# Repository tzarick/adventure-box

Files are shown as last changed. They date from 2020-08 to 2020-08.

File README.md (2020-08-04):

# adventure-box

A box that only opens / unlocks when it arrives at specific geographic coordinates.

## Disclaimer

If you are one of the few people I gave one of these boxes to and you still haven't reached your destination _and_ you somehow found this... 1) get a move on with it smh, and 2) leave now!!! Be gone! Mild spoilers live here.

## Background

This project was made as a Christmas gift for each member (each couple, technically) of my family: a lockbox that is locked when they unwrap it and only openable once they take it with them to some specific location on the globe. I thought it would be a fun reverse geocache / scavenger hunt.

I like the idea of "opening" the box as an adventure / experience rather than seeing it as just a thing in a box that requires some extra work to open.

## Functionality

The small display on the outside of the box shows:

1. the **distance** in miles away from the destination, and
2. the **heading** in degrees that you need to proceed in

This specific program currently takes in 2 sets of coordinates:

1. a final destination, and
2. a checkpoint

Initially, the checkpoint is treated as the destination (the user should not know this, as all they see is a distance and heading, and know that they need to take the box somewhere). At the checkpoint, there was a physical clue in real life which eventually prompted them to interact with the box in a way that passes the checkpoint and reveals their new distance and heading (to the final destination).

Upon arrival at the final destination, the 3-digit box combination is displayed on-screen.

## Hardware / Parts

Main box components:

- 3-digit combination aluminum lockbox
- 128 x 64 OLED display
- NEO-6M GPS module + antenna
- Arduino Pro Mini 5V
- Piezo buzzer
- Push button
- Power switch
- Small 5V/1A power bank
- USB charging cable

I'll include a full list of the specific parts I used at a later time (TODO).

## Software

I consulted some examples / projects from the NEO-6M GPS module and projects that involve both GPS module and small I2C OLED display. I also found some specific piezo buzzer note encodings and a short sequence or two online. Will include specific references at a later time (TODO).

Am going to clean up the code a bit, hopefully soon (TODO).

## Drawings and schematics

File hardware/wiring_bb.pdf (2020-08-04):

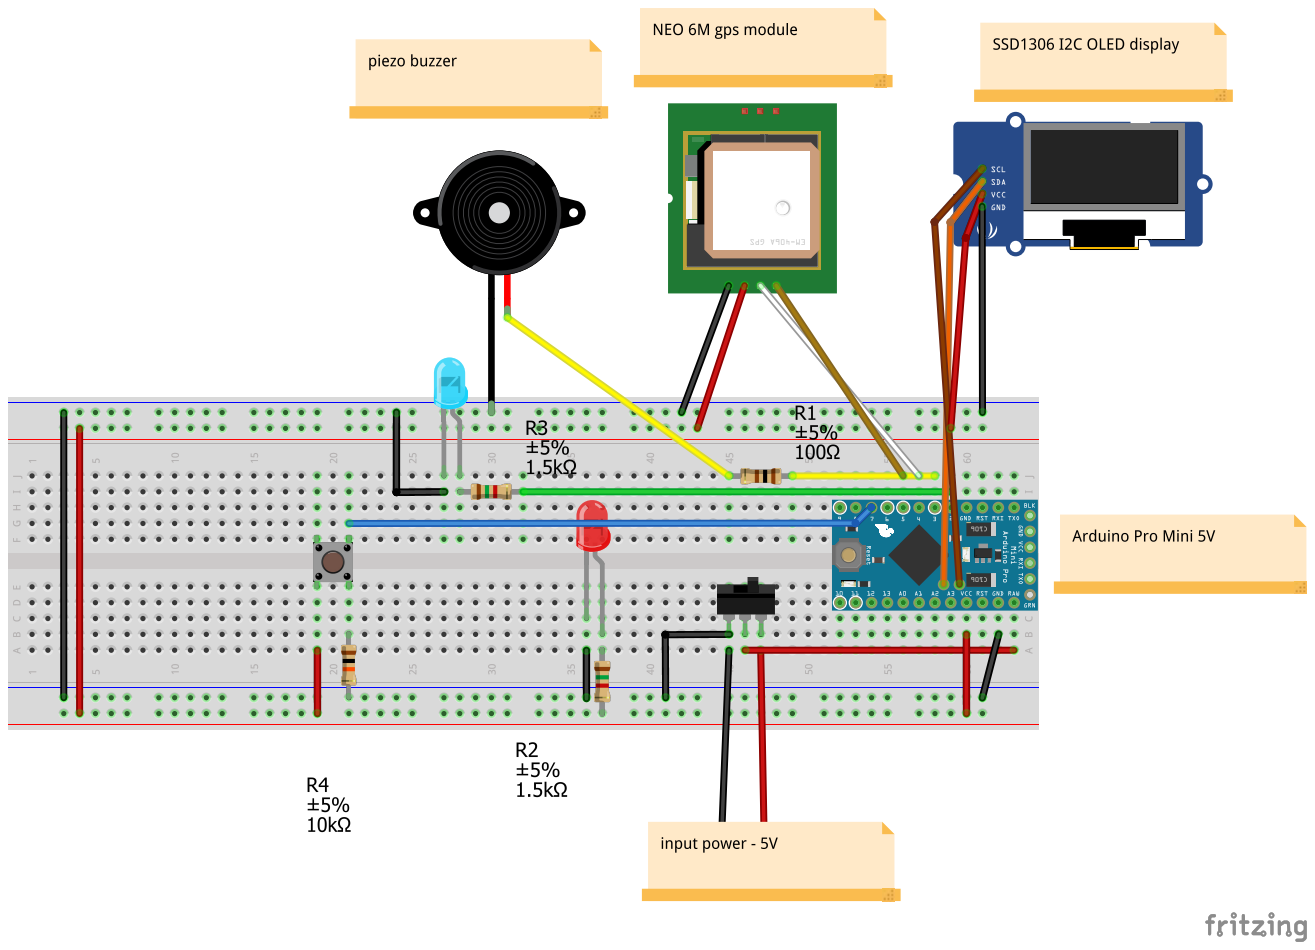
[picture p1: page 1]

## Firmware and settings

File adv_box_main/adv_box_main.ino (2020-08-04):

#include <EEPROM.h>
#include <TinyGPS++.h>
#include <SoftwareSerial.h>
//#include <AltSoftSerial.h>
//#include <SPI.h>
#include <Wire.h>
#include <Arduino.h>
#include <U8x8lib.h>

#ifdef U8X8_HAVE_HW_SPI
#include <SPI.h>
#endif

// chest sound params
int speakerPin = 3;
const int switchPin = 1;
const int buttonPin = 7;
const int fixLed = 2;

char notes[] = "gabygabyxzCDxzCDabywabywzCDEzCDEbywFCDEqywFGDEqi        azbC"; // a space represents a rest
int length = sizeof(notes); // the number of notes
int beats[] = { 1,1,1,1, 1,1,1,1, 1,1,1,1, 1,1,1,1, 1,1,1,1, 1,1,1,1, 1,1,1,1, 1,1,1,1, 1,1,1,1, 1,1,1,1, 1,1,1,1, 1,1,1,1, 1,1,1,1, 1,1,1,1, 2,3,3,16,};
int tempo = 75;

char notes_poke_heal[] = "bbbgG";
int length_poke = sizeof(notes_poke_heal);
int beats_poke_heal[] = { 4,4,2,2,3 };
int tempo_poke = 80;

enum { // distance status
  ACQUIRING,
  RLY_FAR,
  FAR,
  CLOSER,
  ON_FIRE,
  ARRIVED
};

enum { // journey_status
  XMAS_MORN,
  NO_PROGRESS,
  CHECKPOINT_ARRIVED,
  CHECKPOINT_COMPLETED,
  DESTINATION_ARRIVED
};


int cur_status = ACQUIRING;

int journey_status = EEPROM.read(0); // last session's arrival status is saved in addr 0 of EEPROM --> already fully completed journey if this loc contains DESTINATION_ARRRIVED (3)

// gps setup
SoftwareSerial ss(4,5);
//AltSoftSerial altSerial;
TinyGPSPlus gps;

// display init
U8X8_SSD1306_128X64_NONAME_SW_I2C u8x8(/* clock=*/ SCL, /* data=*/ SDA, /* reset=*/ U8X8_PIN_NONE);   // OLEDs without Reset of the Display

// coords define
#define CHECKPOINT_LAT 00.00000   // actual coords redacted !
#define CHECKPOINT_LNG 00.00000
#define FINAL_LAT 00.0000
#define FINAL_LNG 00.00000

#define COMBINATION XXX // combination to the three number lock box code. actual combination redacted !

#define UNIQUE_BUTTON_HOLD_TIME 7000  // this is the amount of time (ms) the button needs to be held to pass the 1st first checkpoint (when in proximity of the checkpoint location)

#define milesInKm 0.62137119223
#define feetInMile 5280.0

const double checkpointTarget[2] = {CHECKPOINT_LAT, CHECKPOINT_LNG};
const double finalTarget[2] = {FINAL_LAT, FINAL_LNG};
bool flag_checkpoint_just_completed = false;
double targetLat;
double targetLng;



void playTone(int tone, int duration) {
  for (long i = 0; i < duration * 1000L; i += tone * 2) {
    digitalWrite(speakerPin, HIGH);
    delayMicroseconds(tone);
    digitalWrite(speakerPin, LOW);
    delayMicroseconds(tone);
  }
}

void playNote(char note, int duration) {
  char names[] = { 'c', 'd', 'e', 'f', 'g', 'x', 'a', 'z', 'b', 'C', 'y', 'D', 'w', 'E', 'F', 'q', 'G', 'i' };
  // c=C4, C = C5. These values have been tuned.
  int tones[] = { 1898, 1690, 1500, 1420, 1265, 1194, 1126, 1063, 1001, 947, 893, 843, 795, 749, 710, 668, 630, 594 };
   
  // play the tone corresponding to the note name
  for (int i = 0; i < 18; i++) {
    if (names[i] == note) {
      playTone(tones[i], duration);
    }
  }
}

void playChestSound() {
    if (digitalRead(switchPin) == 1) {
      for (int i = 0; i < length; i++) {
        if (notes[i] == ' ') {
          delay(beats[i] * tempo); // rest
        } else {
          playNote(notes[i], beats[i] * tempo);
        }
          
        // pause between notes
        delay(tempo / 2); 
    }
  }
}

void playPokeSound() {
    if (digitalRead(switchPin) == 1) {
    for (int i = 0; i < length_poke; i++) {
      if (notes_poke_heal[i] == ' ') {
        delay(beats_poke_heal[i] * tempo); // rest
      } else {
        playNote(notes_poke_heal[i], beats_poke_heal[i] * tempo_poke);
      }
        
      // pause between notes
      delay(tempo_poke / 2); 
    }
  }
}


void arrivalRoutine() {
  playChestSound();
  digitalWrite(fixLed, LOW);
  // display combination
  u8x8.setCursor(0,4);
  u8x8.print("Code:");
  u8x8.setCursor(6,4);
  u8x8.print(COMBINATION);
}


void setup() {
//  EEPROM.write(0,0);
  u8x8.begin(); // display setup
  u8x8.setPowerSave(0); 
  u8x8.setFont(u8x8_font_chroma48medium8_r);
  

  if (journey_status != DESTINATION_ARRIVED) {
      Serial.begin(9600);
    //  if(!display.begin(SSD1306_SWITCHCAPVCC, 0x3C)) {
    //    Serial.println(F("SSD1306 display screen allocation failed"));
    //  }
      Serial.println("start");
      targetLat = (journey_status >= CHECKPOINT_COMPLETED) ? finalTarget[0] : checkpointTarget[0];
      targetLng = (journey_status >= CHECKPOINT_COMPLETED) ? finalTarget[1] : checkpointTarget[1];

    //  altSerial.begin(9600);
      ss.begin(9600);

       if (journey_status == XMAS_MORN) {
          u8x8.print("Merry X-mas");
          u8x8.setCursor(0,1);
          u8x8.print("Nicky & Liv!! :)");
          u8x8.setCursor(0,4);
          u8x8.print("Love, Tommy");
       }
       else if (journey_status == CHECKPOINT_ARRIVED) { // arrived at checkpoint but haven't completed it yet
          u8x8.drawString(0,0,"Acquiring...");
          u8x8.setCursor(0,4);
          u8x8.print("You made it!");
          u8x8.setCursor(0,5);
          u8x8.setInverseFont(1);
          u8x8.print("go down ravine.");
          u8x8.setInverseFont(0);
          u8x8.setCursor(0,6);
          u8x8.print("Enter the mouth");
          u8x8.setCursor(0,7);
          u8x8.print("50 paces 4 hint");
      }
      else {
        u8x8.drawString(0,0,"Acquiring...");
      }
      
      u8x8.refreshDisplay();  
    
    
      pinMode(speakerPin, OUTPUT);
      pinMode(switchPin, INPUT);
      pinMode(fixLed, OUTPUT);
      digitalWrite(fixLed, LOW);
      digitalWrite(switchPin, HIGH);
  }
  else { // game over from here on out forever

      u8x8.print("You rock!");
      u8x8.setCursor(0,2);
      u8x8.print("Merry Xmas :)");
      u8x8.setCursor(0,4);
      u8x8.print("Code:");
      u8x8.setCursor(6,4);
      u8x8.print(COMBINATION);
      while(1); // nothing forever
  }


}

void loop() {
    digitalWrite(fixLed, LOW);
    
    if (journey_status == XMAS_MORN && digitalRead(buttonPin) == HIGH) { // xmas morning initial button press
      journey_status = NO_PROGRESS;
      EEPROM.write(0,journey_status);

      // update display
      u8x8.clear();
      u8x8.drawString(0,0,"Acquiring...");
      u8x8.refreshDisplay();
    }
    
    unsigned long button_press_instant = millis(); 
    while (journey_status == CHECKPOINT_ARRIVED && digitalRead(buttonPin) == HIGH) {
      if (millis() - button_press_instant > UNIQUE_BUTTON_HOLD_TIME) { // checkpoint complete!!
        ss.end(); // stop bc of interference with pwm/buzzer
        
        playPokeSound();
        
        ss.begin(9600);
        
        // update destination and journey status
        journey_status = CHECKPOINT_COMPLETED;
        EEPROM.write(0, journey_status);
        flag_checkpoint_just_completed = true;
        
        targetLat = finalTarget[0];
        targetLng = finalTarget[1];
        
        // update display with the limited amount of characters we have to work with on this tiny display
        u8x8.clearLine(4);
        u8x8.clearLine(5);
        u8x8.clearLine(6);
        u8x8.clearLine(7);
        u8x8.setCursor(0,4);
        u8x8.print("Nice work!u pass");
        u8x8.setCursor(0,5);
        u8x8.print("the checkpoint!!");
        u8x8.setCursor(0,6);
        u8x8.print("Next stop: ur");
        u8x8.setCursor(0,7);
        u8x8.print("actual dst!:)");
        u8x8.refreshDisplay();
      }
    }
    
    while (ss.available() > 0 && cur_status != ARRIVED && journey_status > XMAS_MORN){
     
    // get the byte data from the GPS
    byte gpsData = ss.read();
    gps.encode(gpsData);
    if (gps.location.isUpdated()){
      digitalWrite(fixLed, HIGH); // GPS led indicator
      Serial.println();

      // get location and distance from gps data
      double *coords = getLocation(); 
      Serial.println(coords[1], 6);
      Serial.println(coords[0], 6);
      double distance = distanceToTarget(coords[0], coords[1], targetLat, targetLng); 
      double distanceToX =
        TinyGPSPlus::distanceBetween(
          gps.location.lat(),
          gps.location.lng(),
          targetLat, 
          targetLng); // in meters
      double courseToX =
        TinyGPSPlus::courseTo(
          gps.location.lat(),
          gps.location.lng(),
          targetLat, 
          targetLng);

      // sanity check
      Serial.print("distance:   ");
      Serial.println(distance, 6);
      double mi = kmToMiles(distanceToX/1000);
      Serial.println(mi, 6);
      double f = milesToFeet(mi);
      Serial.println(f, 6);
      Serial.print("distTo: ");
      Serial.println(distanceToX/1000, 6);
      Serial.print("course to: ");
      Serial.println(courseToX, 6);

      
      u8x8.setFont(u8x8_font_chroma48medium8_r);
      u8x8.setCursor(0,0);
      u8x8.print("Distance away:");
      u8x8.setCursor(0,1);
      u8x8.print(mi, 6);
      u8x8.print(" mi");
      u8x8.setCursor(0,2);
      u8x8.print("Head:");
      u8x8.setCursor(0,3);
      u8x8.print(courseToX, 6);
      u8x8.print(" deg");
      u8x8.refreshDisplay(); 
      
      if (f < 300) {
        // congrats and display code
        if (journey_status == NO_PROGRESS) { // arrived at checkpoint but haven't completed it yet
          // update journey status and screen with extra hint
          u8x8.clearLine(4);
          u8x8.clearLine(5);
          u8x8.clearLine(6);
          u8x8.clearLine(7);
          u8x8.setCursor(0,4);
          u8x8.print("You made it!");
          u8x8.setCursor(0,5);
          u8x8.print("go down ravine.");
          u8x8.setCursor(0,6);
          u8x8.print("Enter the mouth");
          u8x8.setCursor(0,7);
          u8x8.print("50 paces 4 hint");
          u8x8.refreshDisplay();
          journey_status = CHECKPOINT_ARRIVED;
          EEPROM.write(0, journey_status);
        }
        else if (journey_status == CHECKPOINT_COMPLETED){ // arrival at final target destination
          u8x8.clear();
          u8x8.print("Arrived!!!! :D");
          u8x8.setCursor(0,1);
          u8x8.print("CONGRATS");
          u8x8.setCursor(0,2);
          u8x8.print("NICKY & LIV!!!"); // this should be dynamically populated
          u8x8.refreshDisplay();
          ss.end();
          arrivalRoutine();
          cur_status = ARRIVED;
          EEPROM.write(0, DESTINATION_ARRIVED); // point of no return. Everything is different now
        }

      }
      else if (mi < 1) {
        if (cur_status != ON_FIRE) {
          if (journey_status >= CHECKPOINT_COMPLETED) {
            u8x8.clearLine(5);
            u8x8.setCursor(0,5);
            u8x8.print("Good job so far!");
          }
          u8x8.clearLine(6);
          u8x8.setCursor(0,6);
          u8x8.print("You're on fire!!");
          u8x8.setCursor(0,7);
          u8x8.print("Sooooo close...");
          u8x8.refreshDisplay();
          cur_status = ON_FIRE;
        }
      }
      else if (mi < 10) {
        if (cur_status != CLOSER) {
          if (journey_status >= CHECKPOINT_COMPLETED) {
            u8x8.clearLine(5);
            u8x8.setCursor(0,5);
            u8x8.print("Good job so far!");
          }
          u8x8.clearLine(6);
          u8x8.clearLine(7);
          u8x8.setCursor(0,6);
          u8x8.print("Can you smell it");
          u8x8.setCursor(0,7);
          u8x8.print("????????");
          u8x8.refreshDisplay();
          cur_status = CLOSER;
        }
      }
      else if (mi < 100) {
        if (cur_status != FAR) {
          if (journey_status >= CHECKPOINT_COMPLETED) {
            u8x8.clearLine(5);
            u8x8.setCursor(0,5);
            u8x8.print("Good job so far!");
          }
          u8x8.clearLine(6);
          u8x8.clearLine(7);
          u8x8.setCursor(0,6);
          u8x8.print("Getting warmer.");
          u8x8.setCursor(0,7);
          u8x8.print("Keep it up! :)");
          u8x8.refreshDisplay();
          cur_status = FAR;
        }
      }
      else {
        if (cur_status != RLY_FAR) {
          if (!flag_checkpoint_just_completed) {
            if (journey_status >= CHECKPOINT_COMPLETED) {
              u8x8.clearLine(5);
              u8x8.setCursor(0,5);
              u8x8.print("Good job so far!");
            }
            u8x8.clearLine(6);
            u8x8.clearLine(7);
            u8x8.setCursor(0,6);
            u8x8.print("Pretty far away.");
            u8x8.setCursor(0,7);
            u8x8.print("Get moving! :0");
            u8x8.refreshDisplay();
          }
            cur_status = RLY_FAR; 
        }
      }
    }
    Serial.write(gpsData);
  }
}

double * getLocation() {
  static double loc[2];

  loc[0] = gps.location.lat();
  loc[1] = gps.location.lng();
  
  return loc;
}

double milesToFeet(double mi) {
  return mi * feetInMile;
}

double kmToMiles(double km) {
  return km * milesInKm;
}

// convert degrees to radians
double degToRad(double degree) {
  return degree * PI/180;
}

// distance between 2 geographical coordinates in km
double distanceToTarget(double lat1, double lng1, double lat2, double lng2) {
  double earthRadius = 6371; // m
  
  double distLat = degToRad(lat2 - lat1);
  double distLng = degToRad(lng2 - lng1);
  
  double lat1_rad = degToRad(lat1);
  double lat2_rad = degToRad(lat2);

  double a = sin(distLat / 2) * sin(distLat / 2) + cos(lat1_rad) * cos(lat2_rad) * sin(distLng / 2) * sin(distLng / 2);
  double c = 2 * atan2(sqrt(a), sqrt(1-a));

  return earthRadius * c;
}

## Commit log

2020-08-04 initial + cleanup
    [wiring.fzz]
2020-08-04 add wiring
    [wiring.fzz]
2020-08-04 component labels and bread board diagram
    [wiring.fzz]
2020-08-04 I2C typo
    [wiring.fzz]
